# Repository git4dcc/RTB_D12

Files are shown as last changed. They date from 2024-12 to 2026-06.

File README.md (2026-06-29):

# RTB_D12




My Homebrew [D12](https://rtb4dcc.de/hardware/decoder/d12/) decoder is a drop in replacement for the original analog FLM (#7230) PCB. The decoder is designed to integrate into the [RTB](https://rtb4dcc.de/concept/) digital control infrastructure.

<details>
<summary>See also</summary>

- [RTB_D13 - custom](/../../../../git4dcc/RTB_D13) (Minitrix coach)
- [RTB_D15 - custom](/../../../../git4dcc/RTB_D15) (Minitrix V160)
- [RTB_D16 - NEM651](/../../../../git4dcc/RTB_D16)
- [RTB_D20 - NEM651](/../../../../git4dcc/RTB_D20)
- [RTB_D21 - Next18](/../../../../git4dcc/RTB_D21)
- [RTB_D22 - Plux16](/../../../../git4dcc/RTB_D22)
- [RTB_D23 - NEM652](/../../../../git4dcc/RTB_D23)

</details>

<details>
<summary>User Guides</summary>

- User Guide - DE
- [User Guide - EN](https://rtb4dcc.de/rtb_decoder_reference_en/)

</details>

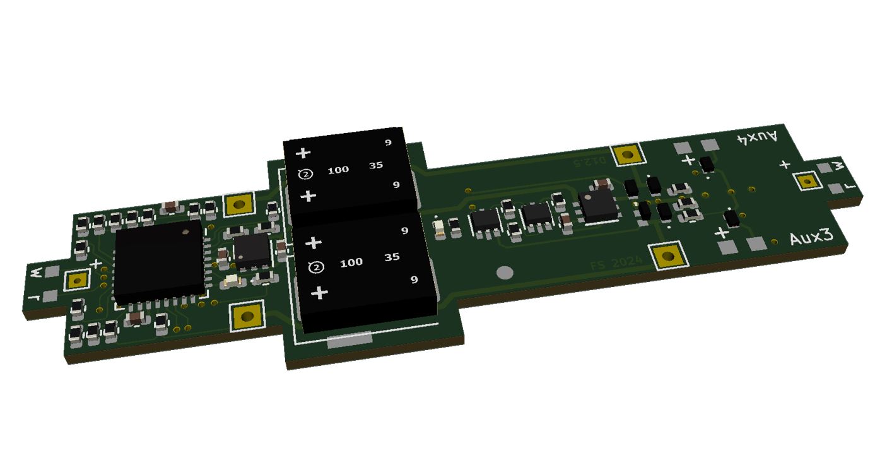
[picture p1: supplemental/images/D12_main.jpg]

<br>

## Decoder features
- **Fleischmann V100** PCB decoder
- **DCC**
  - DCC-A automatic logon
  - DCC-R protocol extension
  - Service Mode Programming
- **Railcom**
  - Channel 1/2
  - POM, xPOM
  - DYN: Speed, QoS, Track-voltage, Motor-current, AUX-current, Temp, Distance travelled
- 7-18V track voltage
- heartbeat LED
- adjustable max motor current (default 250mA)
- adjustable max AUX current (default 250mA)
- over temp protection
- Function output: LF/LR (dimmable, 1.4kHz), LED on PCB
- Function output: AUX1/AUX2 (dimmable, 1.4kHz) logic level (3.3V)
- Function output: AUX3/AUX4 open drain
- Function output: AUX5 cabin light, LED on PCB
- buffer capacitor 2x330uF
- <10mA idle power consumption
- Firmware update over main tracks via DCC-R protocol

# Hardware
The current PCB layout uses SMD footprints with 0.5mm pitch and mainly 0603 parts. Reflow soldering is recommended whereas handsoldering will be difficult.

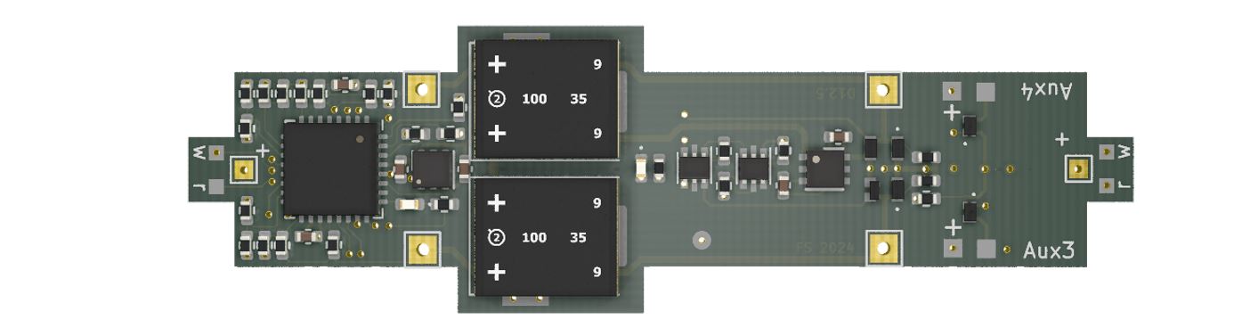
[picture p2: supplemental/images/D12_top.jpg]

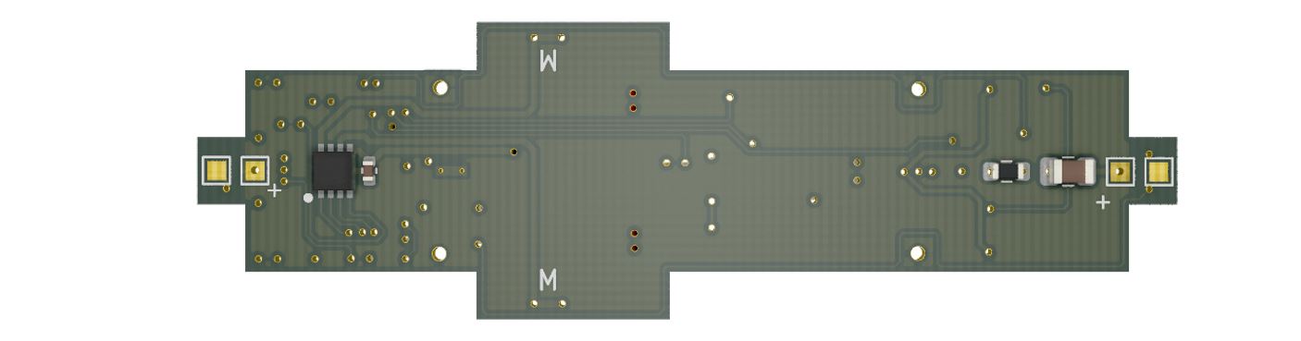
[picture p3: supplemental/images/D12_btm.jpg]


## PCB
- 4-layer PCB, FR4, 0.8mm
- CPU: AVR64DA32
- Motor bridge: DRV8231
- Inrush limiter: R/D combination

## Kicad
[Schematic](doc/D12_schematic.pdf) | [Layout](doc/D12_layout.pdf)

The BOM is tailored to JLCPCB part#.

<details>
<summary>Dependency</summary>
<br>

:yellow_circle: Requires my Kicad project library [RTB_SamacSys](https://github.com/git4dcc/RTB_SamacSys) in the same directory tree.

</details>

## Firmware
Filename structure: { **pcb** }{ **code** }{ **version** }.hex

Example: **D12F0001**.hex

| | Description |
| --- | --- |
| **pcb** | Name of matching hardware (**D12**) |
| **code** | Type of code contained (**R**=rom, **B**=bootloader, **F**=flash, **U**=bld update, **P**=UPDI factory code) |
| **version** | Release version (**####**) |

[Firmware files](firmware)

# Images
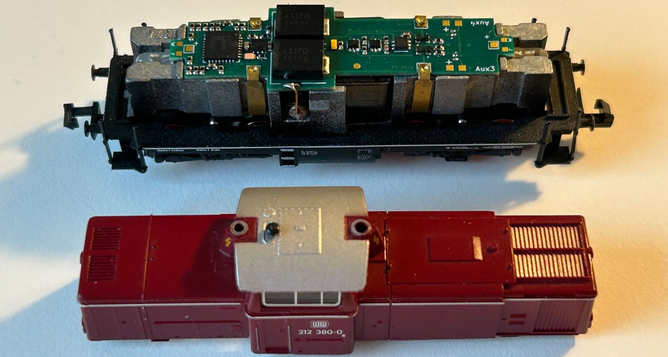
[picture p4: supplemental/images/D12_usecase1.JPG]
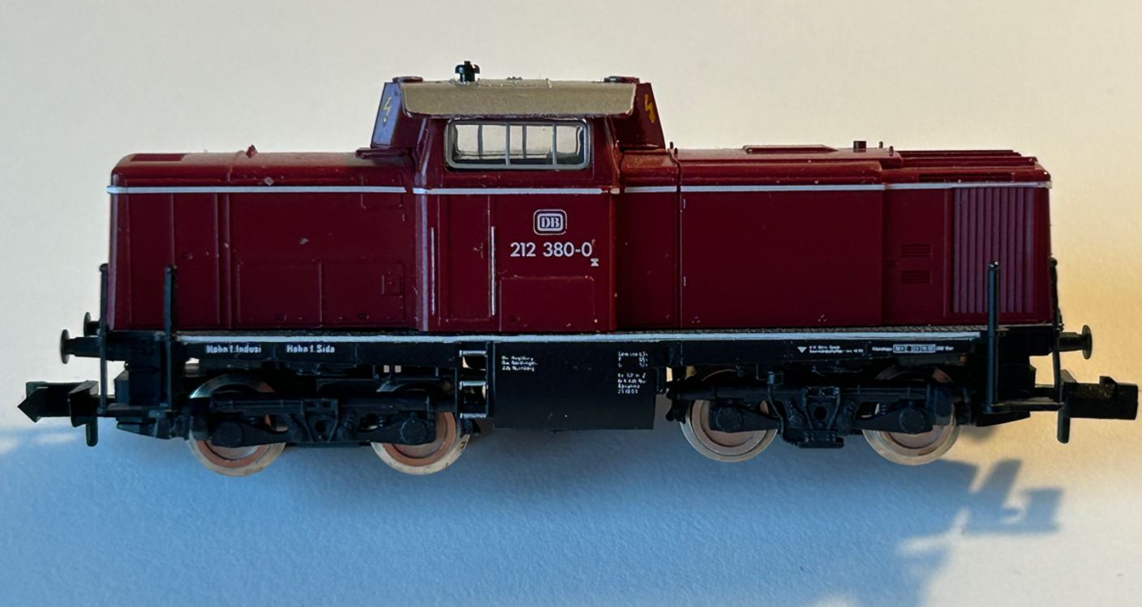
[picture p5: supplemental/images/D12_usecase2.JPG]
 

# YouTube
See the D12 decoder in action.<br><br>
[](https://youtu.be/G0pOsj4374I)

This project is intended for hobby use only and is distributed in accordance with the Apache License 2.0 agreement.

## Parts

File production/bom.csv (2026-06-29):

Designator | Footprint | Quantity | Value | LCSC Part #
C1 | 0402 | 1 | 100n/50V | C307331
C11, C13 | 0402 | 2 | 10u/6.3V | C15525
C12 | 0805 | 1 | 47uF/6.3V | C16780
C2, C3 | CP_EIA-7361-38_AVX-V | 2 | 330u/20V
C22 | 0402 | 1 | 1u | C52923
C4 | 0402 | 1 | 4.7u/25V | C2858031
C5 | 0402 | 1 | 100n | C307331
D1, D2, D4, D6, D7, D8, D9 | SM5819L2TP | 7 | SM5819L2-TP | C6297199
D3 | 0402 | 1 | LED | C74342
D5 | 0402 | 1 | LED | C130724
IC1 | SON50P200X200X80-9N | 1 | DRV8231ADSGR | C5139865
IC2 | WSON-6-1EP_2x2mm_P0.65mm_EP1x1.6mm_ThermalVias | 1 | NCP730BMT500TBG | C892822
J1, J20, J21, J5, J8, J9 | TestPoint_Pad_1.0x1.0mm | 6 | Conn_01x01
J10 | Solder 2.0 x 0.8 | 1 | Motor A
J11 | Solder 2.0 x 0.8 | 1 | Motor B
J12, J14 | Solder 0.8 x 0.8 | 2 | Vtrk
J13 | Solder 0.8 x 0.8 | 1 | AUX4.od
J15 | Solder 0.8 x 0.8 | 1 | AUX3.od
J16 | Solder 0.8 x 0.8 | 1 | Aux1
J17 | Solder 0.8 x 0.8 | 1 | Aux2
J18, J19 | Solder 0.8 x 0.8 | 2 | Conn_01x01
J2, J3, J4, J6 | TestPoint_THTPad_1.5x1.5mm_Drill0.7mm | 4 | Conn_01x01
J7 | Solder 0.8 x 0.8 | 1 | UDPI
Q1 | SOT-666 | 1 | BC857BDW1 | C282521
Q2 | SOT-666 | 1 | BC847BDW1 | C455062
Q3, Q4 | PMZB200UNEYL | 2 | PMZB200UNEYL | C547292
R1 | 0402 | 1 | 1k | C11702
R10, R12, R21, R5, R6 | 0402 | 5 | 33k | C25779
R11, R13 | 0402 | 2 | 12k | C25752
R15, R18, R19, R20 | 0402 | 4 | 10k | C25744
R2, R24, R25, R4 | 0402 | 4 | 2.2k | C25879
R22, R23 | 0402 | 2 | 3.3k | C25890
R3 | 0402 | 1 | 22 | C25092
R34, R35, R9 | 0402 | 3 | 220k | C25767
R36, R37 | 0402 | 2 | 9.1k | C25926
R7 | 0603 | 1 | 1 | C22936
R8 | 0402 | 1 | 68 | C25076
U1 | VQFN-32-1EP_5x5mm_P0.5mm_EP3.1x3.1mm | 1 | AVR-64DA32 | C3225673

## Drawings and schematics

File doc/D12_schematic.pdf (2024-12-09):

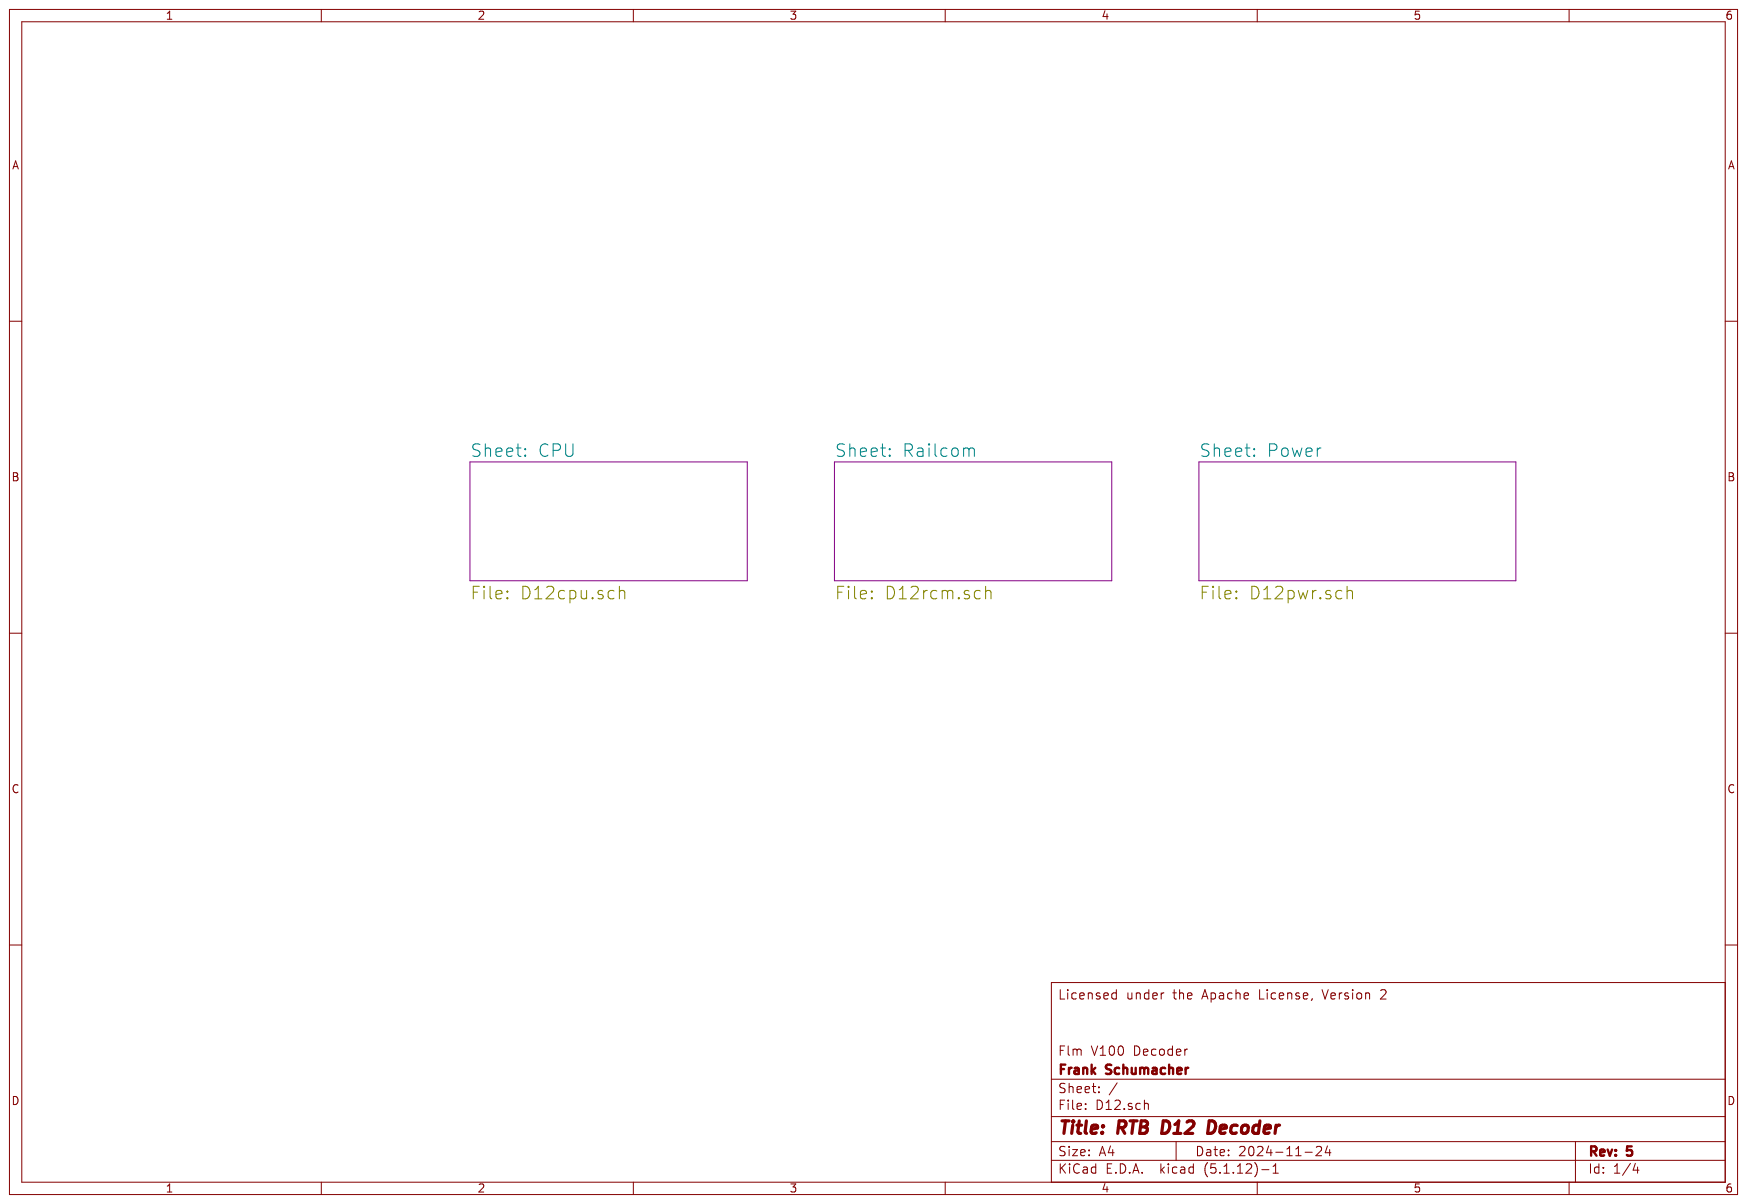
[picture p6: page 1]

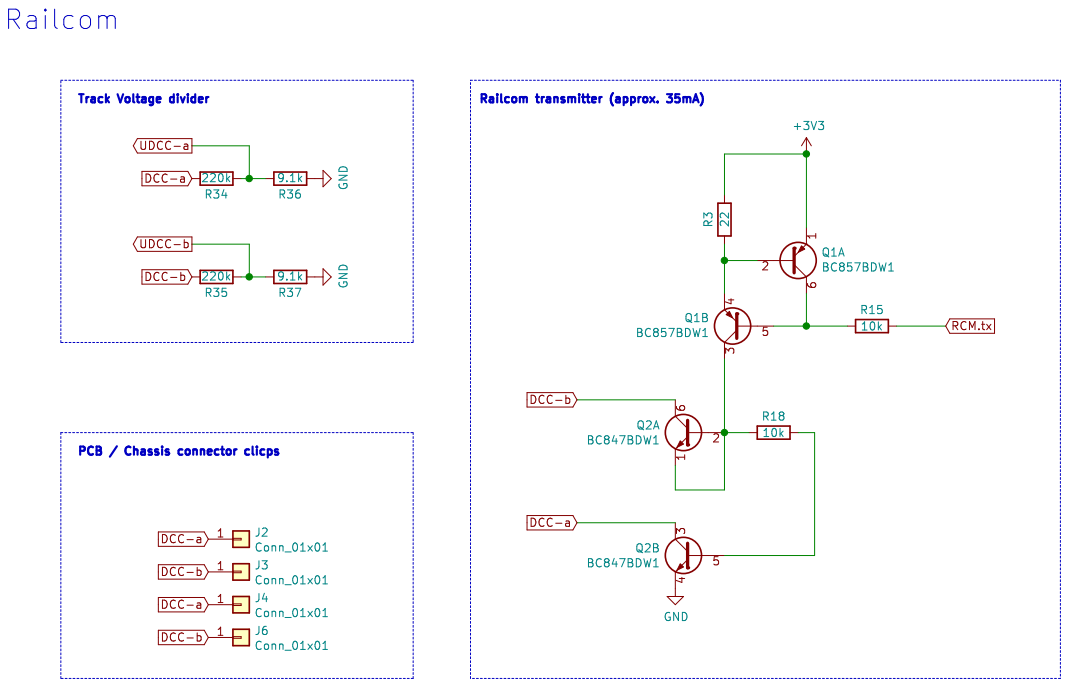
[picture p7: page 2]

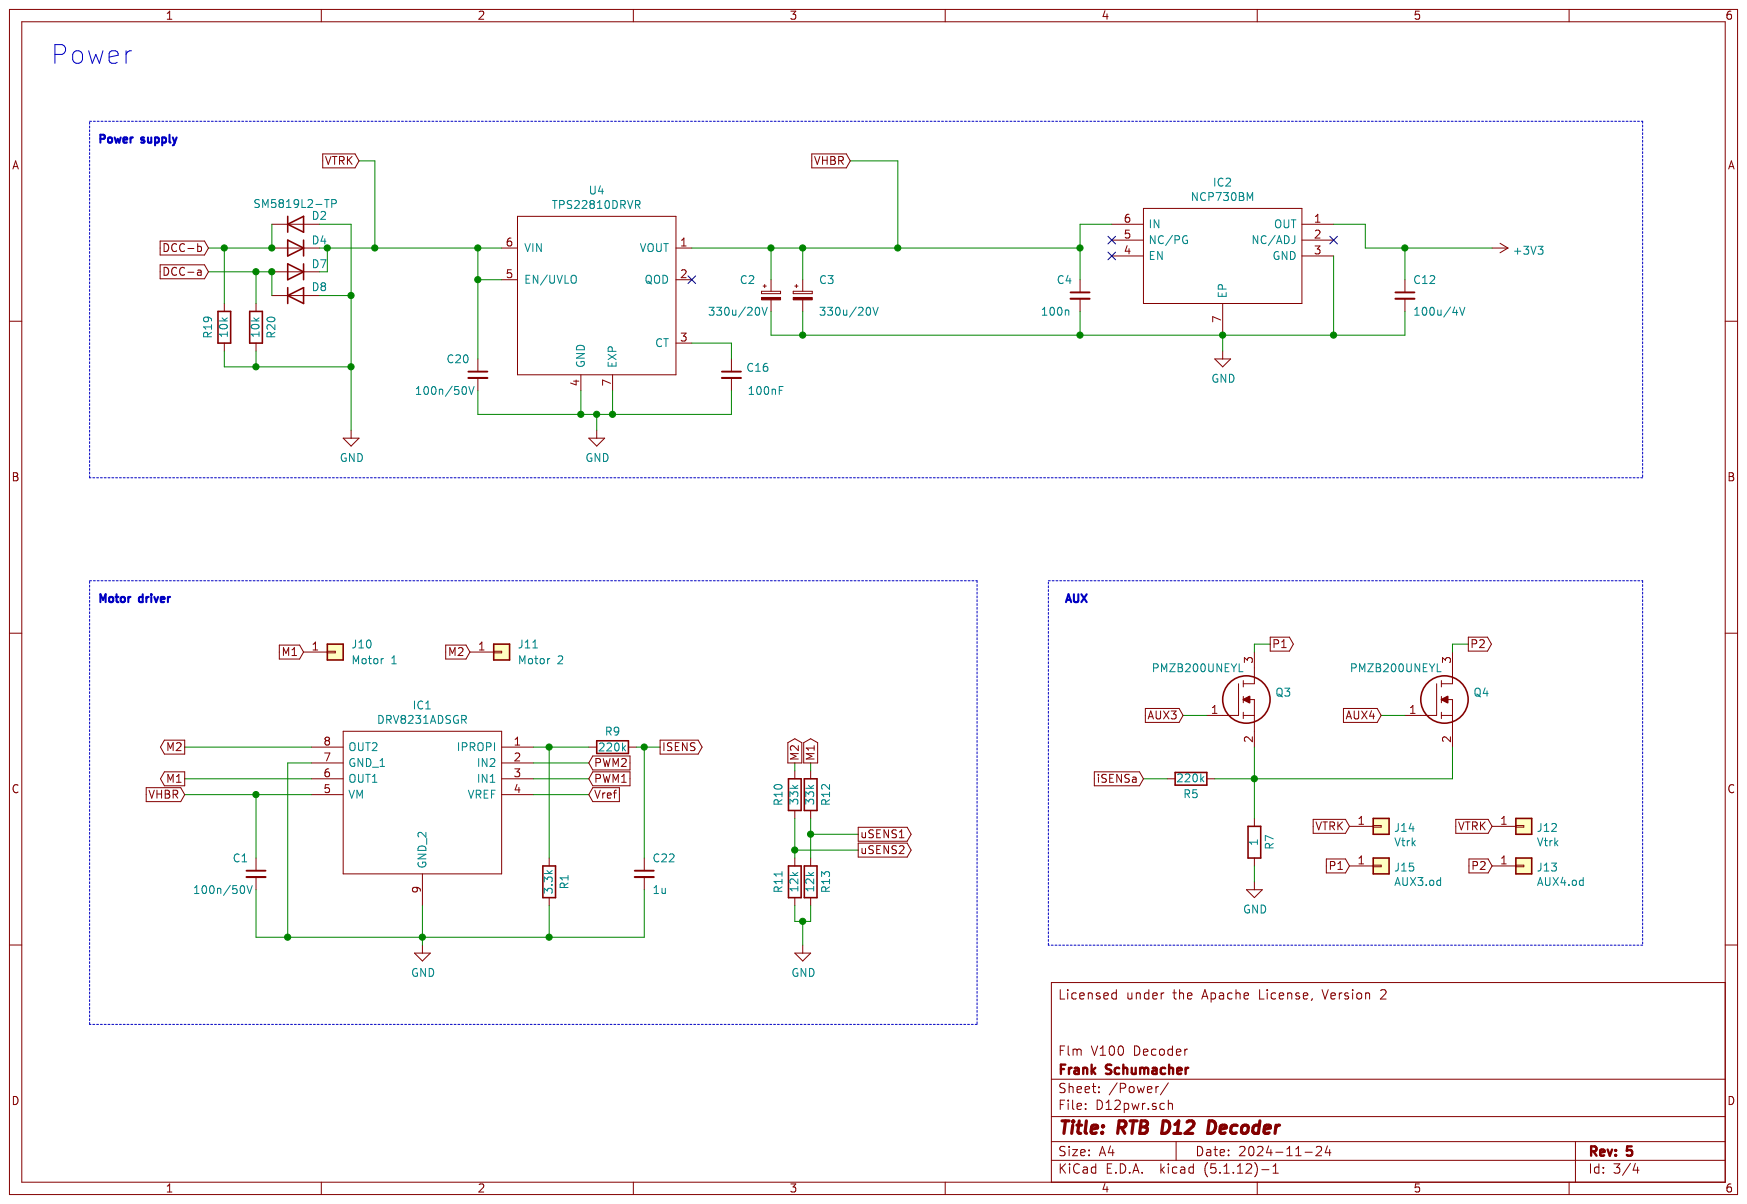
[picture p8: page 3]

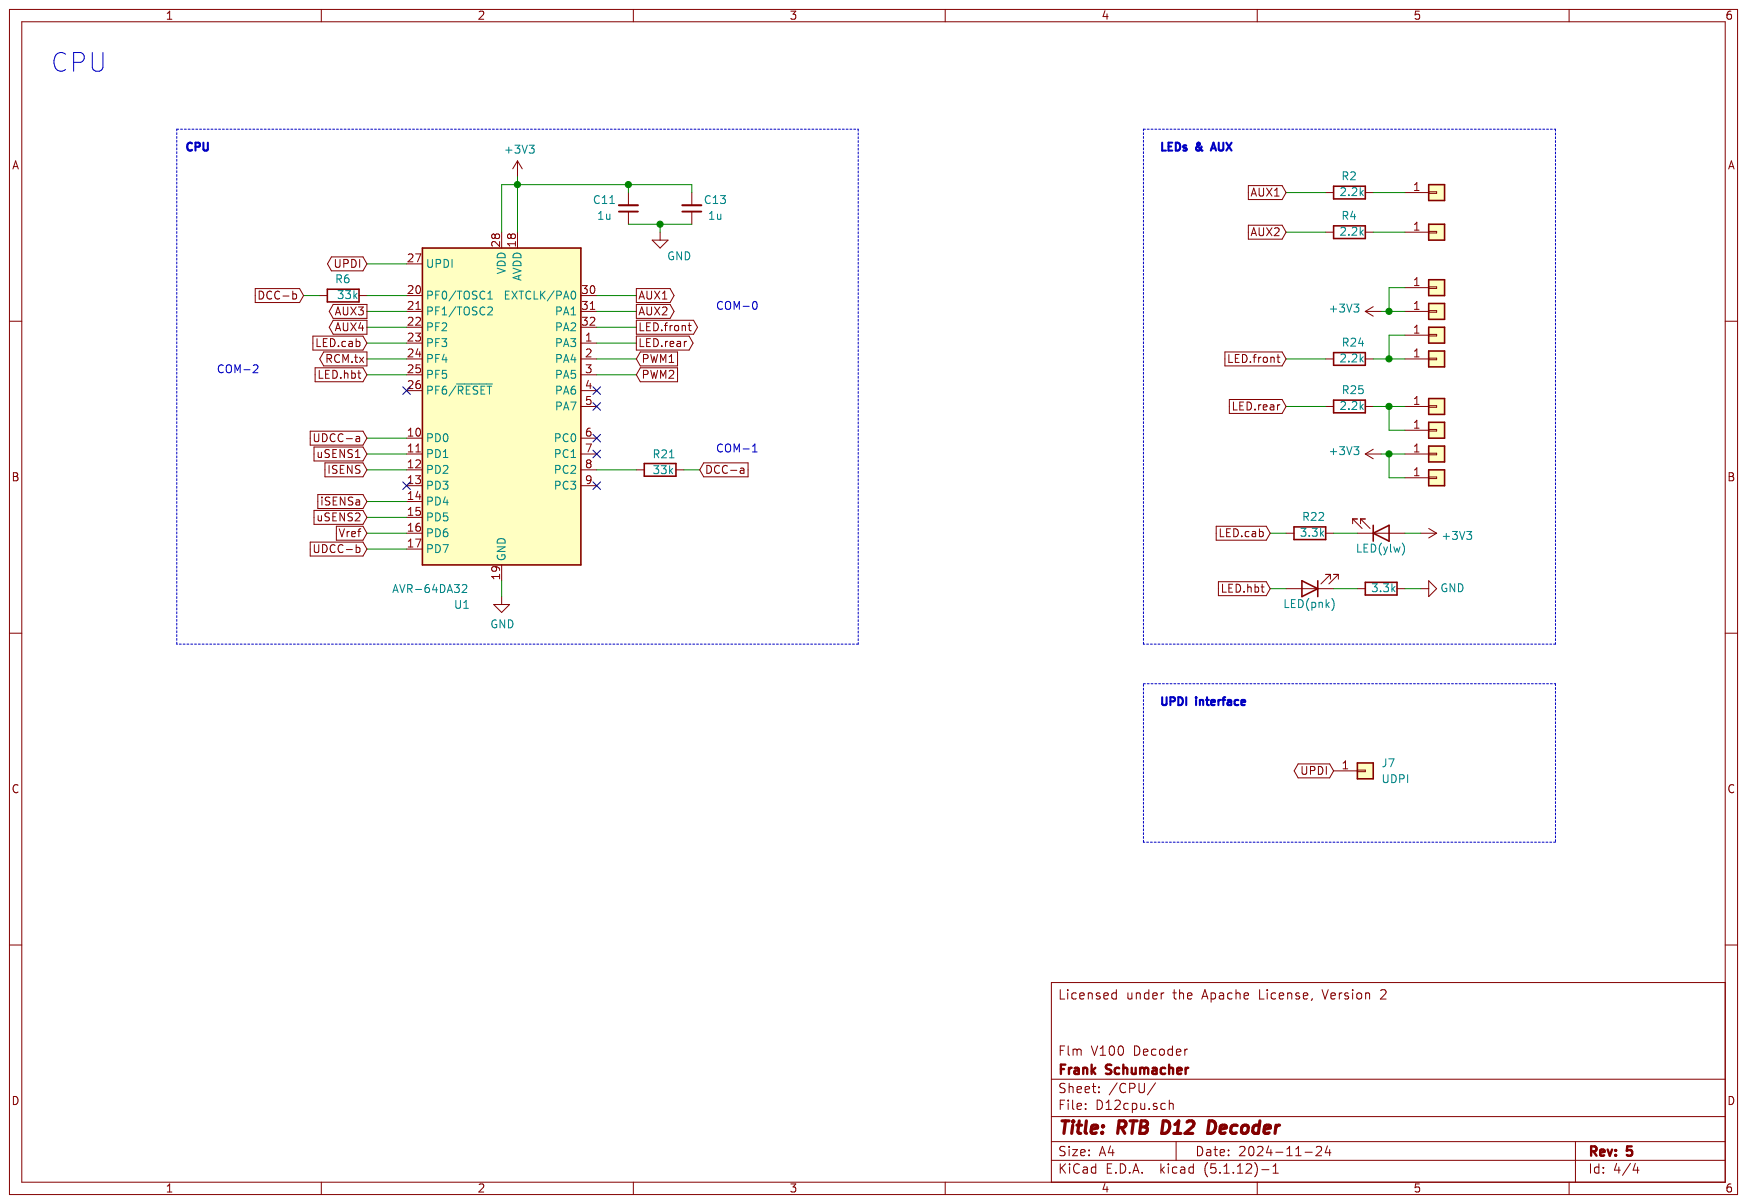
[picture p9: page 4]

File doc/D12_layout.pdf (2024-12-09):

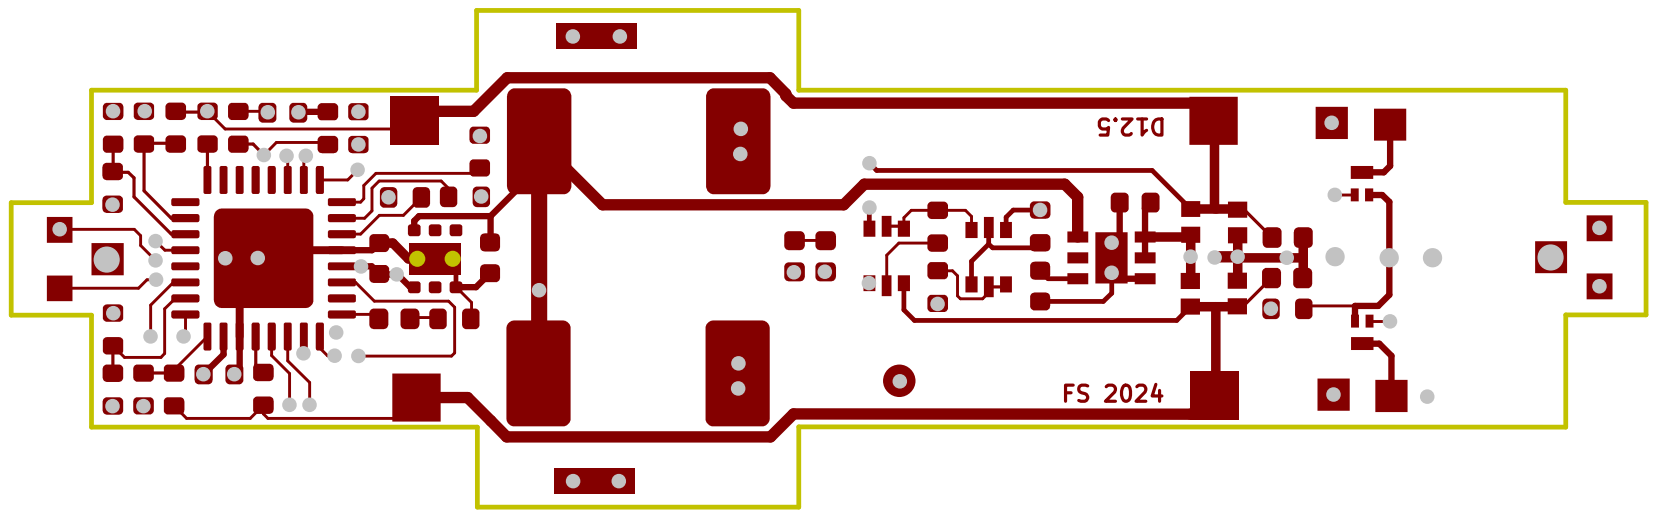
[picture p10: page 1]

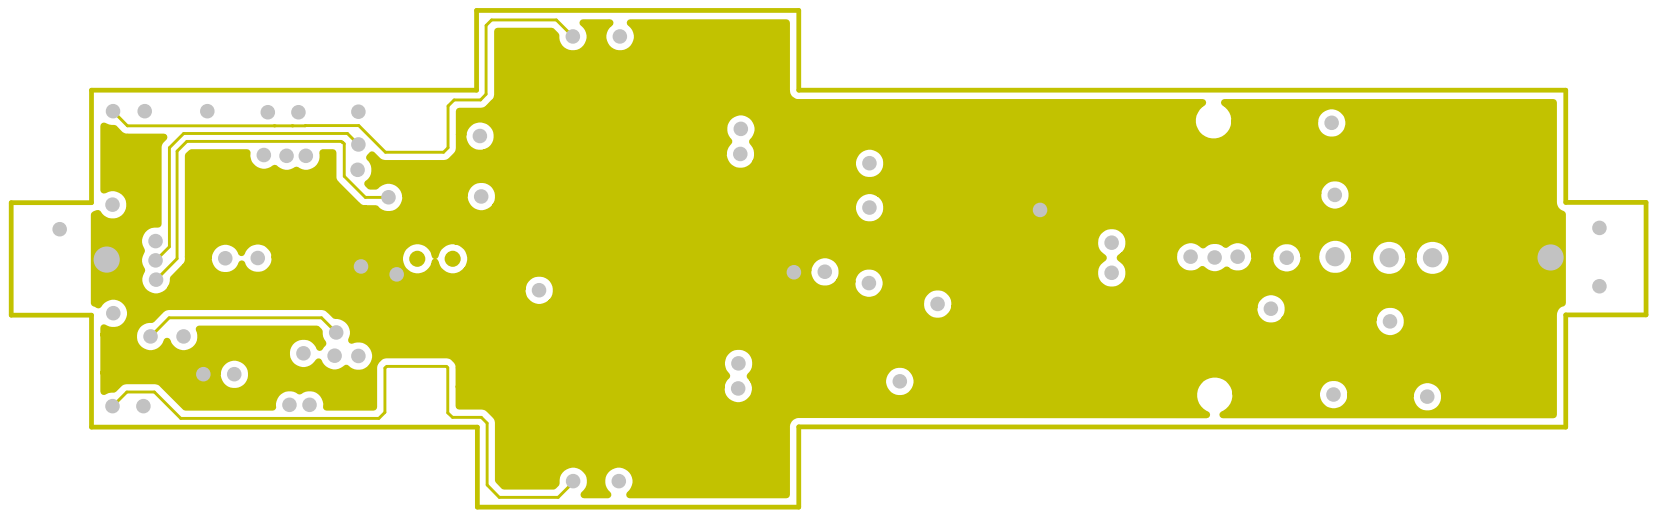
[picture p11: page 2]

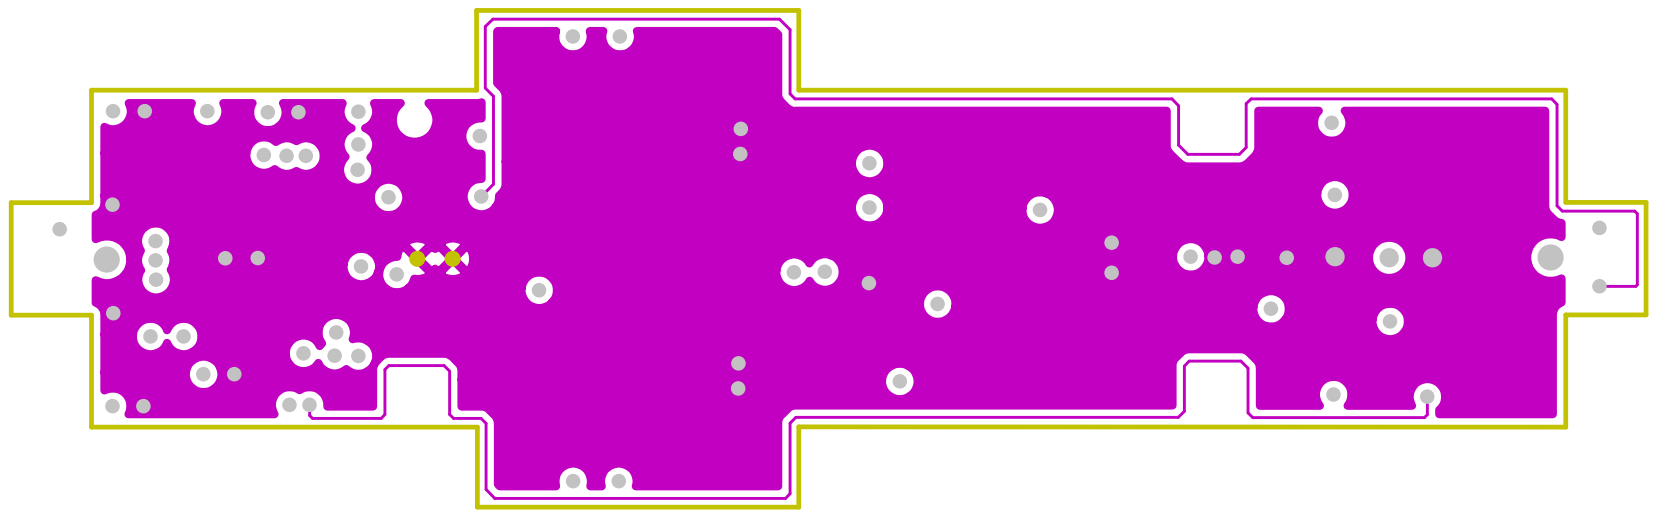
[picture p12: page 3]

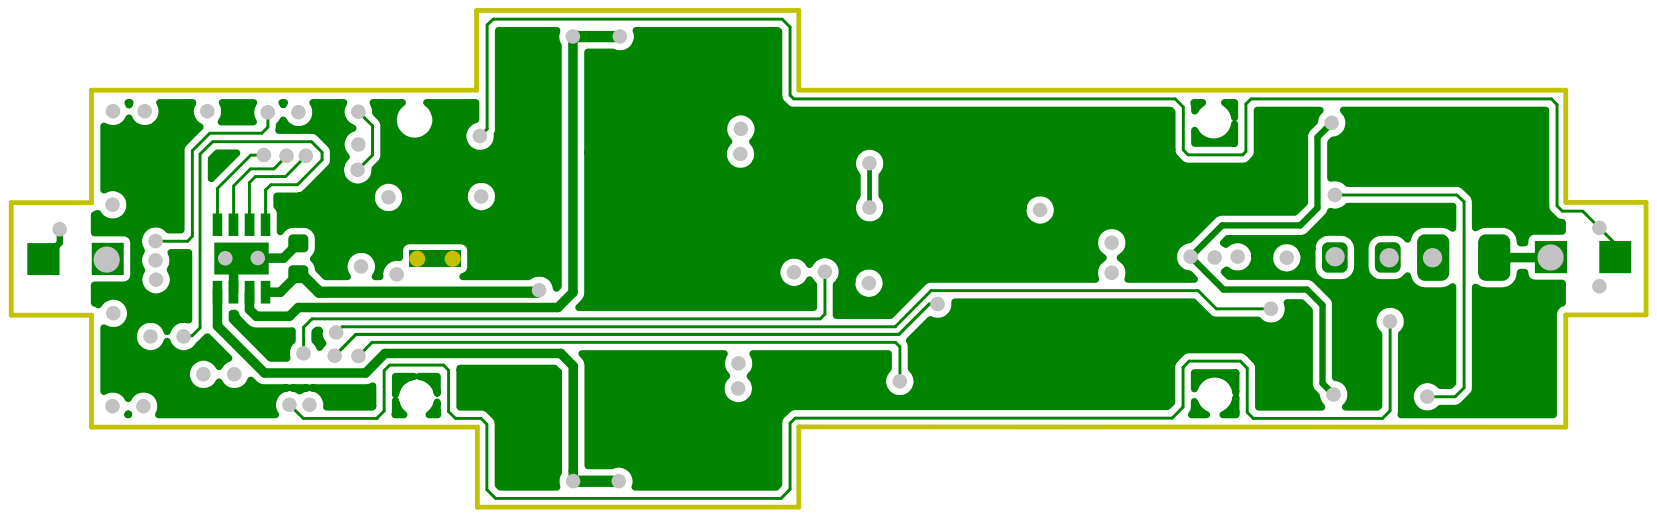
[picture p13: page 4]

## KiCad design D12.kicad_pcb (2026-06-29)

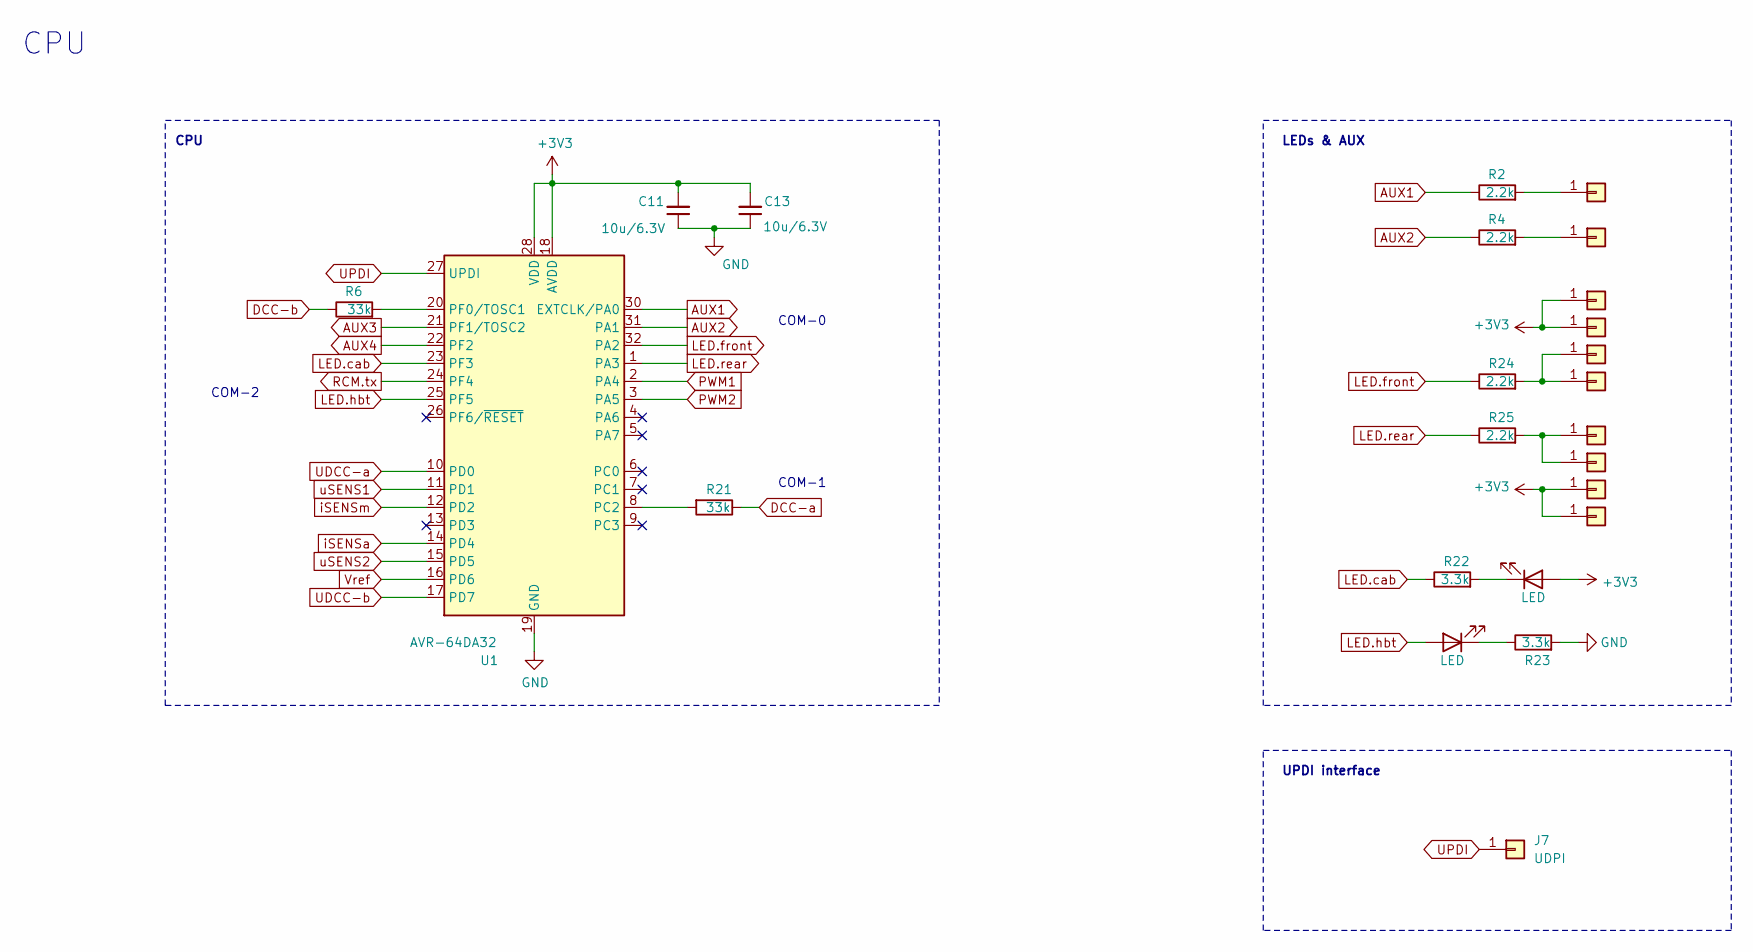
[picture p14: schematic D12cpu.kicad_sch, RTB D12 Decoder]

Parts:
C11, C13: 10u/6.3V; C_0402_1005Metric; LCSC Part # C15525
D3: LED; LED_0402_1005Metric; LCSC Part # C74342
D5: LED; LED_0402_1005Metric; LCSC Part # C130724
J1, J5, J8, J9, J20, J21: Conn_01x01; TestPoint_Pad_1.0x1.0mm
J7: UDPI; Solder 0.8 x 0.8
J16: Aux1; Solder 0.8 x 0.8
J17: Aux2; Solder 0.8 x 0.8
J18, J19: Conn_01x01; Solder 0.8 x 0.8
R2, R4, R24, R25: 2.2k; R_0402_1005Metric; LCSC Part # C25879
R6, R21: 33k; R_0402_1005Metric; LCSC Part # C25779
R22, R23: 3.3k; R_0402_1005Metric; LCSC Part # C25890
U1: AVR-64DA32; VQFN-32-1EP_5x5mm_P0.5mm_EP3.1x3.1mm; LCSC Part # C3225673

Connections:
+3V3: C11.2, C13.2, D3.2 (A), J8.1 (Pin_1_1), J9.1 (Pin_1_1), J20.1 (Pin_1_1), J21.1 (Pin_1_1), U1.18 (AVDD), U1.28 (VDD); also elsewhere on the board
AUX1: R2.1, U1.30 (EXTCLK/PA0)
AUX2: R4.1, U1.31 (PA1)
AUX3: U1.21 (PF1/TOSC2); also elsewhere on the board
AUX4: U1.22 (PF2); also elsewhere on the board
DCC-a: R21.1; also elsewhere on the board
DCC-b: R6.1; also elsewhere on the board
GND: C11.1, C13.1, R23.2, U1.19 (GND), U1.29 (GND), U1.33 (GND); also elsewhere on the board
LED.cab: R22.1, U1.23 (PF3)
LED.front: R24.1, U1.32 (PA2)
LED.hbt: D5.2 (A), U1.25 (PF5)
LED.rear: R25.1, U1.1 (PA3)
unnamed: D3.1 (K), R22.2
unnamed: D5.1 (K), R23.1
unnamed: J1.1 (Pin_1_1), J18.1 (Pin_1_1), R24.2
unnamed: J16.1 (Pin_1_1), R2.2
unnamed: J17.1 (Pin_1_1), R4.2
unnamed: J5.1 (Pin_1_1), J19.1 (Pin_1_1), R25.2
unnamed: R21.2, U1.8 (PC2)
unnamed: R6.2, U1.20 (PF0/TOSC1)
PWM1: U1.2 (PA4); also elsewhere on the board
PWM2: U1.3 (PA5); also elsewhere on the board
RCM.tx: U1.24 (PF4); also elsewhere on the board
UDCC-a: U1.10 (PD0); also elsewhere on the board
UDCC-b: U1.17 (PD7); also elsewhere on the board
UPDI: J7.1 (Pin_1_1), U1.27 (UPDI)
Vref: U1.16 (PD6); also elsewhere on the board
iSENSa: U1.14 (PD4); also elsewhere on the board
iSENSm: U1.12 (PD2); also elsewhere on the board
uSENS1: U1.11 (PD1); also elsewhere on the board
uSENS2: U1.15 (PD5); also elsewhere on the board

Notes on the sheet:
UPDI interface
COM-1
COM-2
CPU
LEDs & AUX
COM-0

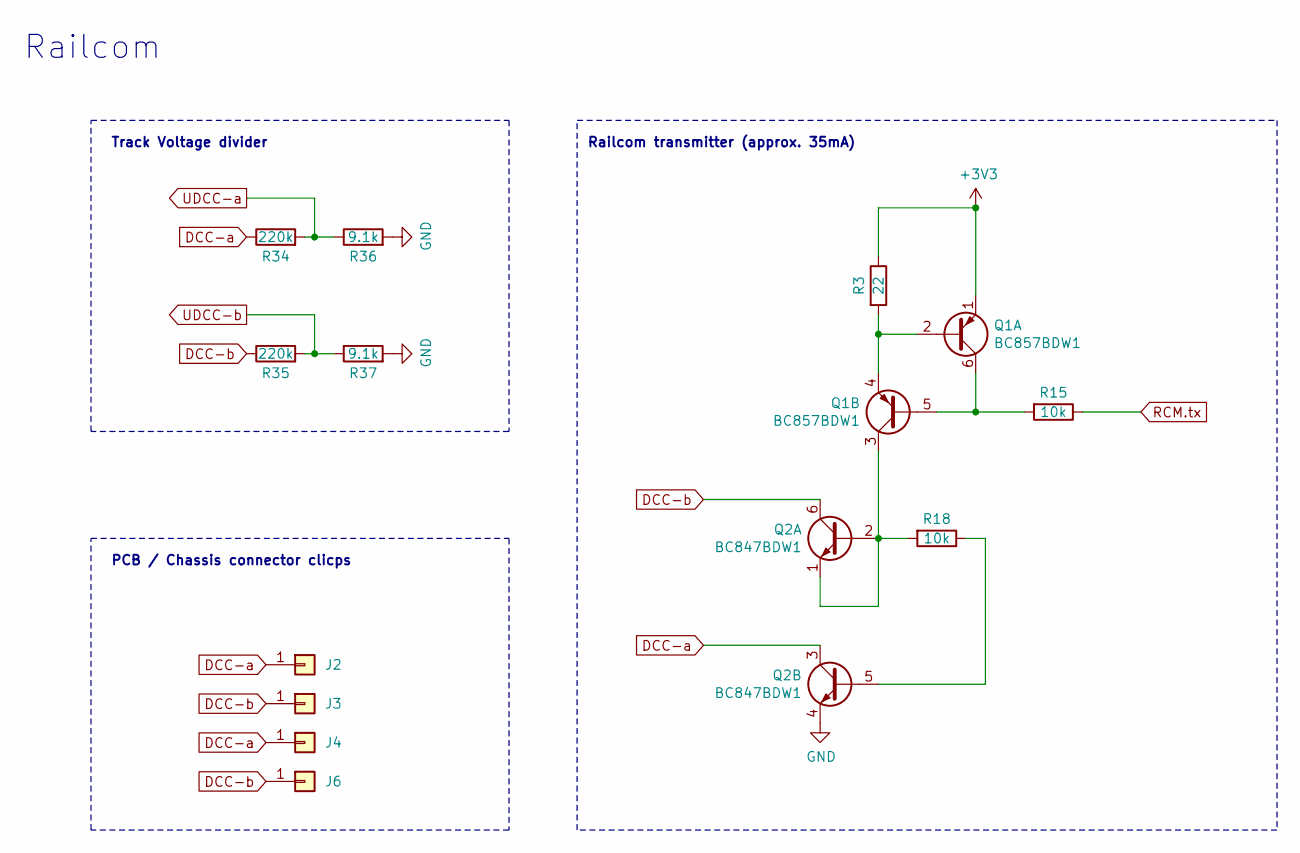
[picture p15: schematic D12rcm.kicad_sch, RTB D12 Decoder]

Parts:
J2, J3, J4, J6: Conn_01x01; TestPoint_THTPad_1.5x1.5mm_Drill0.7mm
Q1: BC857BDW1; SOT-666; LCSC Part # C282521
Q2: BC847BDW1; SOT-666; LCSC Part # C455062
R3: 22; R_0402_1005Metric; LCSC Part # C25092
R15, R18: 10k; R_0402_1005Metric; LCSC Part # C25744
R34, R35: 220k; R_0402_1005Metric; LCSC Part # C25767
R36, R37: 9.1k; R_0402_1005Metric; LCSC Part # C25926

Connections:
+3V3: Q1.1 (E1), R3.1; also elsewhere on the board
DCC-a: J2.1 (Pin_1_1), J4.1 (Pin_1_1), Q2.3 (C2), R34.1; also elsewhere on the board
DCC-b: J3.1 (Pin_1_1), J6.1 (Pin_1_1), Q2.6 (C1), R35.1; also elsewhere on the board
GND: Q2.4 (E2), R36.2, R37.2; also elsewhere on the board
unnamed: Q1.2 (B1), Q1.4 (E2), R3.2
unnamed: Q1.5 (B2), Q1.6 (C1), R15.2
unnamed: Q1.3 (C2), Q2.1 (E1), Q2.2 (B1), R18.2
unnamed: Q2.5 (B2), R18.1
RCM.tx: R15.1; also elsewhere on the board
UDCC-a: R34.2, R36.1; also elsewhere on the board
UDCC-b: R35.2, R37.1; also elsewhere on the board

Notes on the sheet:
PCB / Chassis connector clicps
Railcom transmitter (approx. 35mA)
Railcom
Track Voltage divider

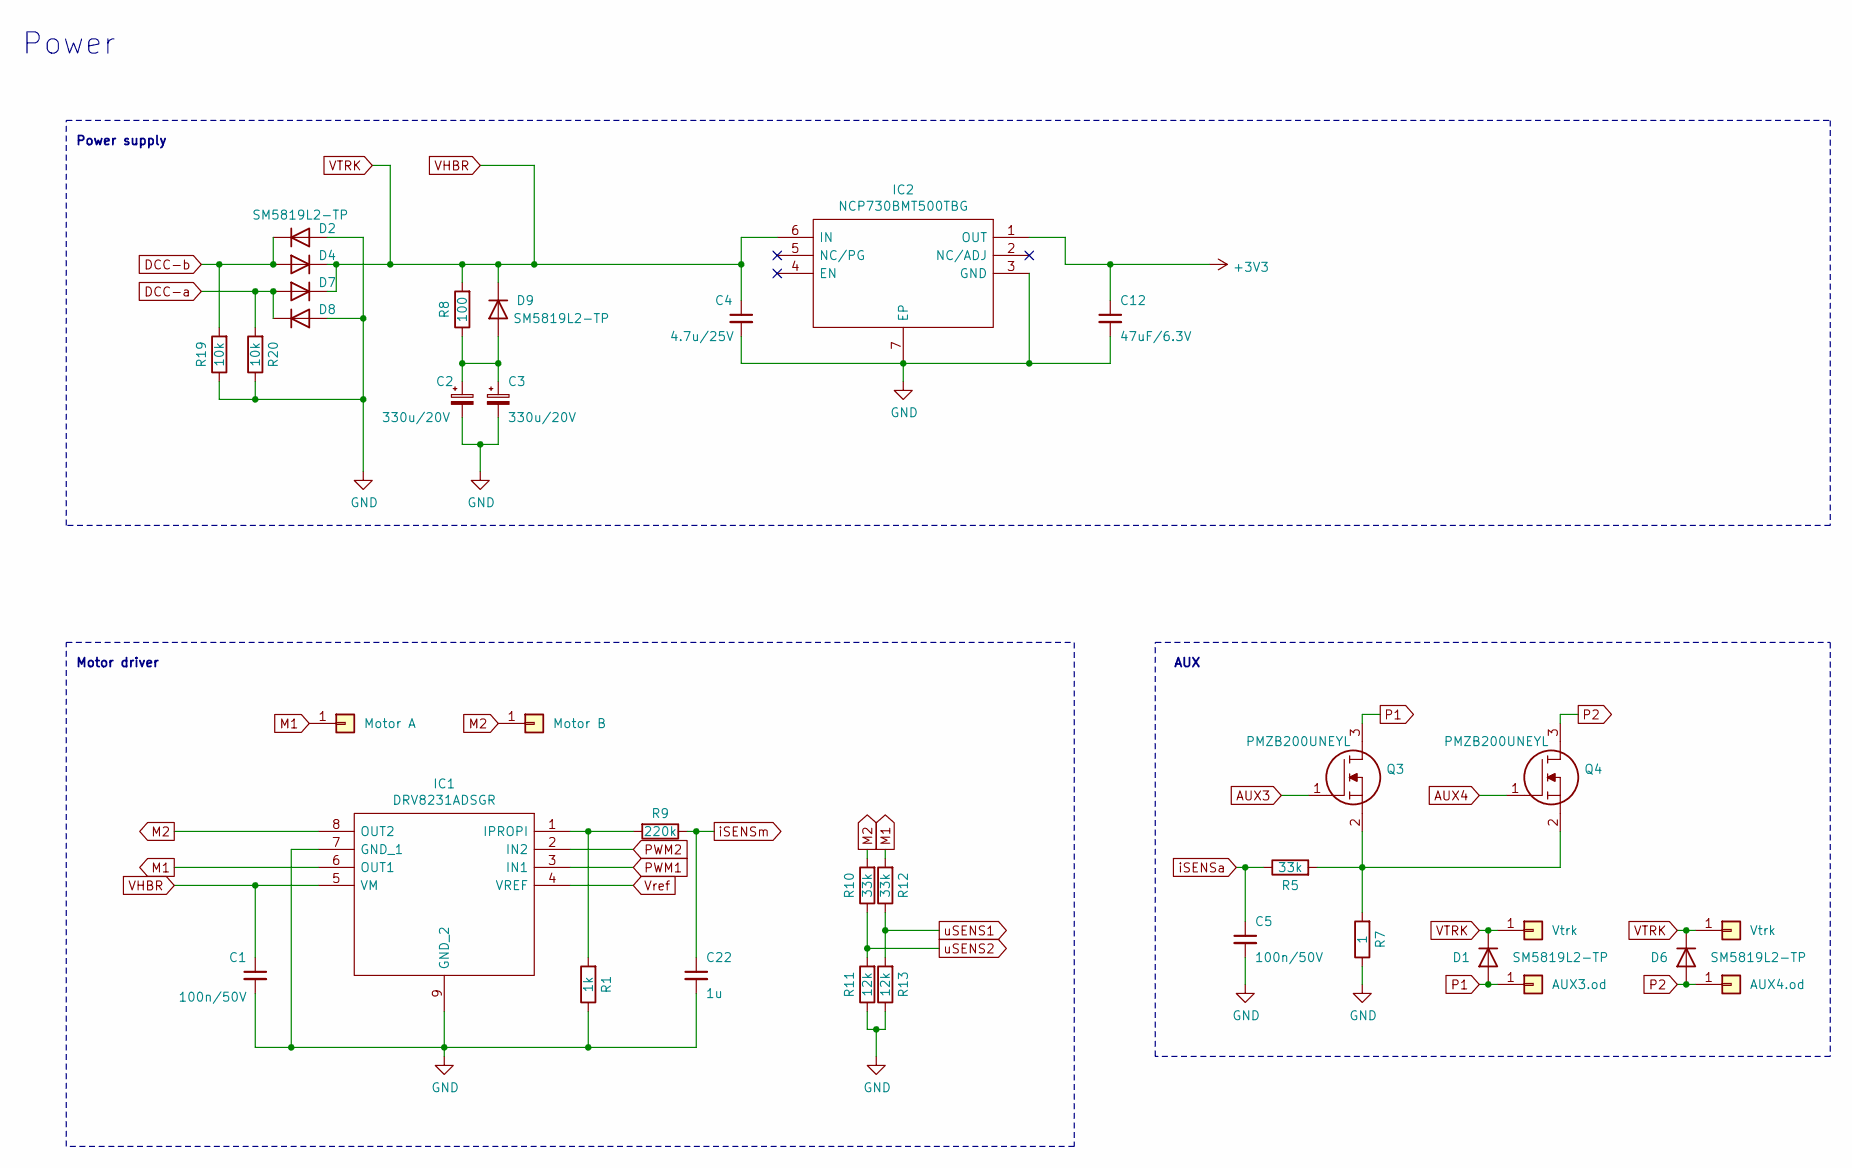
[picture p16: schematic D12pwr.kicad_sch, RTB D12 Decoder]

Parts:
C1, C5: 100n/50V; C_0402_1005Metric; LCSC Part # C307331
C2, C3: 330u/20V; CP_EIA-7361-38_AVX-V
C4: 4.7u/25V; C_0402_1005Metric; LCSC Part # C2858031
C12: 47uF/6.3V; C_0805_2012Metric; LCSC Part # C16780
C22: 1u; C_0402_1005Metric; LCSC Part # C52923
D1, D2, D4, D6, D7, D8, D9: SM5819L2-TP; SM5819L2TP; LCSC Part # C6297199
IC1: DRV8231ADSGR; SON50P200X200X80-9N; LCSC Part # C5139865
IC2: NCP730BMT500TBG; WSON-6-1EP_2x2mm_P0.65mm_EP1x1.6mm_ThermalVias; LCSC Part # C892822
J10: Motor A; Solder 2.0 x 0.8
J11: Motor B; Solder 2.0 x 0.8
J12, J14: Vtrk; Solder 0.8 x 0.8
J13: AUX4.od; Solder 0.8 x 0.8
J15: AUX3.od; Solder 0.8 x 0.8
Q3, Q4: PMZB200UNEYL; LCSC Part # C547292
R1: 1k; R_0402_1005Metric; LCSC Part # C11702
R5, R10, R12: 33k; R_0402_1005Metric; LCSC Part # C25779
R7: 1; R_0603_1608Metric; LCSC Part # C22936
R8: 100; R_0402_1005Metric; LCSC Part # C25076
R9: 220k; R_0402_1005Metric; LCSC Part # C25767
R11, R13: 12k; R_0402_1005Metric; LCSC Part # C25752
R19, R20: 10k; R_0402_1005Metric; LCSC Part # C25744

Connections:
+3V3: C12.1, IC2.1 (OUT); also elsewhere on the board
AUX3: Q3.1; also elsewhere on the board
AUX4: Q4.1; also elsewhere on the board
DCC-a: D7.2 (A), D8.1 (K), R20.2; also elsewhere on the board
DCC-b: D2.1 (K), D4.2 (A), R19.2; also elsewhere on the board
GND: C1.2, C2.2, C3.2, C4.2, C5.2, C12.2, C22.2, D2.2 (A), D8.2 (A), IC1.7 (GND_1), IC1.9 (GND_2), IC2.3 (GND), IC2.7 (EP), R1.1, R7.1, R11.1, R13.1, R19.1, R20.1; also elsewhere on the board
M1: IC1.6 (OUT1), J10.1 (Pin_1_1), R12.2
M2: IC1.8 (OUT2), J11.1 (Pin_1_1), R10.2
unnamed: C2.1, C3.1, D9.2 (A), R8.1
unnamed: IC1.1 (IPROPI), R1.2, R9.2
unnamed: Q3.2, Q4.2, R5.2, R7.2
P1: D1.2 (A), J15.1 (Pin_1_1), Q3.3
P2: D6.2 (A), J13.1 (Pin_1_1), Q4.3
PWM1: IC1.3 (IN1); also elsewhere on the board
PWM2: IC1.2 (IN2); also elsewhere on the board
VHBR: C1.1, C4.1, D1.1 (K), D4.1 (K), D6.1 (K), D7.1 (K), D9.1 (K), IC1.5 (VM), IC2.6 (IN), J12.1 (Pin_1_1), J14.1 (Pin_1_1), R8.2
Vref: IC1.4 (VREF); also elsewhere on the board
iSENSa: C5.1, R5.1; also elsewhere on the board
iSENSm: C22.1, R9.1; also elsewhere on the board
uSENS1: R12.1, R13.2; also elsewhere on the board
uSENS2: R10.1, R11.2; also elsewhere on the board

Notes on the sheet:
Power supply
Motor driver
AUX
Power

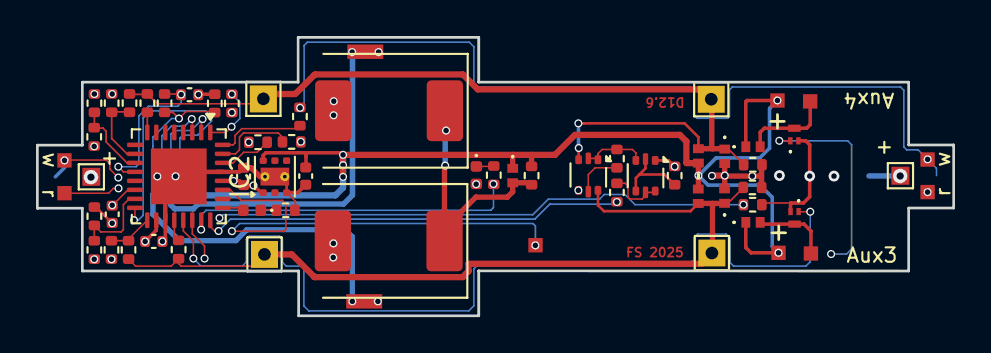
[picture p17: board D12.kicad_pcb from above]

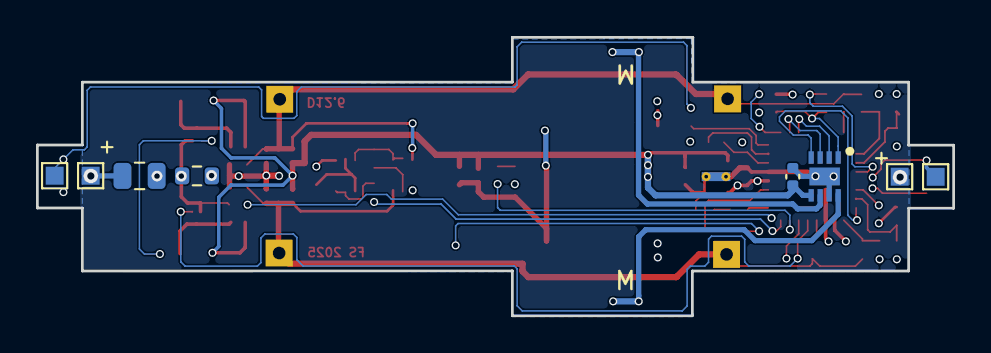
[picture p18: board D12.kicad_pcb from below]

Board: 4 copper layers, 50.9 x 15.5 mm, 72 parts (8 on the bottom side), 43 nets.

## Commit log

2025-03-22 add: decoder lock
    [D12cpu.sch, D12pwr.sch, D12rcm.sch]
2025-08-05 mod: led automation
    [D12.kicad_pcb, D12pwr.sch]
2026-06-29 migrated to Kicad 10
    [D12.kicad_pcb, D12.kicad_sch, D12cpu.kicad_sch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]

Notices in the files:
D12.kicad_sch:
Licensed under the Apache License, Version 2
